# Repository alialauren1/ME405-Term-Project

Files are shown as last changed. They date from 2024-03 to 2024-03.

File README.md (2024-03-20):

# ME405-Term-Project

Our term project this quarter entails constructing a submersible chamber capable of reaching
specified depths. The system will operate in a closed loop, maintaining control until it 
reaches a desired pressure depth.

This project was intended for our senior project where. Dr. Ghalamchi wants to improve previous tests on waterproof drones that can take off from underwater to allow for a drone that can float on top of the water surface as well as have added support to be pushed up from underwater. The new design needs to be detachable from the built waterproof drone to compare its new features in tests. The propellers must also be above the water surface when the drone is idling on the water so that the efficiency of takeoff can be compared to the drone without the chamber in which the whole drone is submerged underwater upon takeoff.

Our project for ME 405 will be the system attached to this drone, enabling the drone to submerge underwater with a minimum depth of 5ft. While allowing for the system to resurface and position the propellers above the water's surface. 

Pressure can be directly correlated to depth, given a liquid's density.
   In order to simulate this system for our ME 405 Term Project, this system takes a desired pressure setpoint and controls a motor-driven syringe system to
   pressurize a chamber to the setpoint. It waits a period of time, as if it were underwater collecting data,
   and then returns to the initial pressure, as if it were returning to the water surface. 

## Hardware design
In Figure 1, we can see the internal system of the system. We have integrated Ametck Pittman's PG6712A077-R3 motor to a 50 CC syringe. Utilizing this motor, we've have attached a worm gear and gears to ensure sufficient torque to be generated. These gears are attached to a pinion
and aligned with a rack that allows for the syringe to be moved back and forth. This allows
for the system to achieve the desired weight to submerge the whole system.

The gears were selected from McMaster. This is so in the future, they can be ordered parts. For now, we used the CAD files to 3D print them for budget reasons. While sizing and choosing the number of teeth we would need for our system, we calculated to torque that the motor needed to have to overcome the friction force between the piston and syringe. This calculation is shown below. In the future, we can order a motor that is more selectively chosen using this information. However for now, we used the motor provided to us in lab. 

$F_r = T_A / R_A$

$T_A = F_R * R_A$

$T_B = T_A$

$T_C = (N_C / N_B ) * T_B$

$T_C = (N_C / N_B ) * (F_R * R_A)$

$T_C = (1/15) * (6 N) * (.0152 m)$

$T_C = (0.006 Nm) = (6 mNm)$ 

Doing these calculations led us to select appropriate gears for our system, ensuring that they can withstand the pressure encountered during operation while maintaining an ideal speed. Below shows a table of the parameters.  

| **Parameters** | Variable | Value | Units |
|:---:|:---:|:---:|:---:|
| **----Rack+Piston+Syringe--** |  **-------** |  **----** |  **----** |
| Force to overcome friction in tube | F_R | 6 | N |
| **----Gears--** |  **-------** | **-----** | **-----** |
| Radius Gear A | R_A | 0.0152  | m |
| Teeth Gear A | N_A | 17 | |
| Outer Diameter Worm Gear B | OD_B | 16 | mm |
| Teeth Worm Gear B | N_B | 15 | |
| Pressure Angle Worm Gear B | Phi_C | 20 |  degrees  |
| Outer Diameter Worm C | OD_C | 12 | mm |
| Pressure Angle Worm C | Phi_C | 20 |  degrees  |
| Teeth Worm C | N_C | 1 | |
| **-----Motor Parameters------**  | **--------** | **-----** |  **----** |
| Radius of Motor Gear | rm |  0.00662  | m |
| Motor Nominal Voltage | V_DC | 12 | V |



Figure 1. CAD: Internal system of our terms project with labels indicating parts of the system.



Figure 2. CAD: Secondary view of the internal system of our terms project with labels indicating parts of the system.

Screenshot 2024-03-19 at 6 15 07 PM

Figure 3. Gears, motor, and frame for the internal system.

The pressure sensor we selected is the SSCMANV030PA2A3 Honeywell Pressure Sensor. It measures absolute pressure, with a range from 0-30 psi. Is allows liquid media on the port, which will come of use in future quarters when we test our system underwater. 

Screenshot 2024-03-19 at 8 53 00 PM

Figure 4. SSCMANV030PA2A3 Honeywell Pressure Sensor



Figure 5. Hardware all connected



Figure 6A. System Connected to Bottom of Drone Body - View 1



Figure 6B. System Connected to Bottom of Drone Body - View 2

Screenshot 2024-03-19 at 8 43 37 PM

Figure 7. Overall View of Drone Body with Chamber 

### Schematic

The schematic below shows a very general diagram of how components are being powered and communicating with one another. 
The power supply provides power to the motor. The power supply was set to 12V with a 0.5 A current limit. 

Schematic

Figure 8. Schematic of components

## Software design
The main program uses three classes inside two tasks that multitask with one another. A detailed description of the software design can be found on our doxygen main page linked here: 
https://alialauren1.github.io/ME405-Term-Project/index.html#soft_org_sec

To measure pressure, we used a Honeywell Board Mount Pressure Sensor, which uses I^2C communication. A class was made to use this sensor. Details on how the data was collected and process is linked below. 
https://alialauren1.github.io/ME405-Term-Project/index.html#autotoc_md1

Attaching the sensor and the Ametek motor to our Nucleo, we were able to program both components to get a functioning product.

### Tasks and States
The Tasks and States used in the main program are shown in diagrams linked on the page below.
https://alialauren1.github.io/ME405-Term-Project/index.html#T_S_sec

## Testing and Results

### Preliminary
Our senior project requires our chamber to be able to acheive at minimum, 5 ft depth. Calculations were run, shown below, to determine the pressure that coincides with a depth of 5 ft in water. Being a little under 16.5 psi, we decided to run initial tests at 16.5 psi.

Screenshot 2024-03-19 at 9 05 30 PM

In order to test our project sensors and motor control, we ran multiple tests in order to find our optimal Kp value. The results are presented in the plot down below. This was preliminary testing. 

Screenshot 2024-03-17 at 10 32 32 PM

Figure 9. Plot of Pressure vs Time inside the syringe. Each line represents a different run of data collected while altering the Kp value.

During our testing, we initially set Kp to 5 (shown in blue) and then increased it to 10 (shown in orange). Observing the graph, it's evident that increasing the Kp value led to faster attainment of the target pressure of 16.5 [psi].

While testing to achieve for efficiency in reaching the desired pressure, it's essential to consider what our system will be attached to. Our system with the syringe and pressure sensor will be attached to a drone. Rapid pressure and volume changes may introduce a moment within the drone body, causing the drone to loose control. Therefore, we must weigh the trade-offs between achieving rapid pressure targets and maintaining system stability.

As we continue to test our project, further tests will be necessary to determine the optimal balance between speed, the system stability and accuracy. This process may involve fine-tuning parameters beyond just changing the Kp. This may incude making the chamber of the system bigger and other factors.

### Lab Demo Results and Functionality of Product
The below plot shows the pressure inside the syringe. The autonomous journey is one in which the system reaches the desired setpoint, waits for a duration, and then returns to the initial pressure. 



Figure 10. Plot of Pressure vs Time inside the syringe with a setpoint of 17 [psi].  

This journey mimics future developement of our larger senior project in which this pressure chamber will be attached to a drone. We anticipate it will be beneficial for some remote or signal to send a desired depth as the setpoint to the system, in which the chamber will submerge with the drone, going to that depth. It will remain there, possible to collect data, and then autonomously return to the surface. 
We are satisfied with the final results. The chamber is able to reach pressures higher than a pressure corresponding to 5ft, which was what we wanted to achieve.
It is also able to maintain the increase in pressure while the motor is turned off, which is a satisfying result. 

The system also works at lower than atmosphere pressures. In the plot below, the setpoint was chosen as 13 psi. However, in another test, we were able run the system with an even lower setpoint of 10 psi. Although this is less necessary to have, it is satisfying to see that ability. 

Screenshot 2024-03-19 at 8 38 33 PM

Figure 11. Plot of Pressure vs Time inside the syringe with a setpoint of 13 [psi].  

## What we have learned
Designing this system taught us how important it is to design and test early. 
Although most of the system was done with a reasonable amount of time, we were faced with issues causing the system to take longer to complete than anticipated.

### 3D Printing
While 3D printing gears and housing system for our project we learned that tolerances while creating parts is harder to achieve. When 3D printing the gears it was harder to align the gears causing the small gears to slip and not allowing for our system to be as efficient as it can be.

Note: We are saving our used PLA parts to find a place to recycle them. 

Screenshot 2024-03-19 at 6 14 47 PM

Figure 12. Collection of gears tested

### Software and Sensors
We learned that the data being output from our pressure sensor was in counts. This led to the creation of a definition in our PressureSensor class to interpret the counts into a unit of measurement that could be easily interpretted, that being [psi]. Since our Closed-Loop Controller class uses the pressure sensor output in counts to correct for a desired pressure, an additional definition was made to interpret user desired setpoint input from [psi] to counts. 

## Safety
Our project prioritizes user safety through thoughtful design considerations. By utilizing small gears, we have effectively reduced the risk of injuries to the user. Once the system has been fully assembled, all moving components and electrical elements will be enclosed and inaccessible to the user. This design ensures that users are protected from potential hazards during the system's operation.

## Bugs and Future Work

We would also like to fix our code in Task2 State 3 where there is a break in data collection between the chamber resting at a higher pressure and then returning to its original pressure. As shown on the plot in the "Lab Demo Results" section, there is a small duration of time in which no data is collected. That is state 3, whilst counter_s3 is between 1 and 3. We tried removing this portion and only having state 3 reset the setpoint to initial pressure in one count but it did not initially work and we have run out of time to work on the code. So, for now, there is that small time duration blip in the data.  

In the future we would like to implement a third task into our main program that is a user interface for the pressure setpoint. 
The user could select from a range of setpoint options and the system would adjust the pressure in the chamber accordingly. 
This task would multitask with the other two tasks and allow for the user to input a setpoint whenever they want whilst the program runs. 

We plan to build a larger waterproof chamber to encompass components similar to those used in project. This will allows us to test the systems depth control abilities in actual water. We look forward to the continuation of this project and appreciate all that it has taught us so far. 

## Additional files

Pressure sensor datasheet:
[SSCMANV030PA2A3 Honeywell.pdf](https://github.com/alialauren1/ME405-Term-Project/files/14630972/SSCMANV030PA2A3.Honeywell.pdf)

I2C Communications with Honeywell Pressure Sensors:
[sps-siot-i2c-comms-digital-output-pressure-sensors-tn-008201-3-en-ciid-45841.pdf](https://github.com/alialauren1/ME405-Term-Project/files/14630975/sps-siot-i2c-comms-digital-output-pressure-sensors-tn-008201-3-en-ciid-45841.pdf)

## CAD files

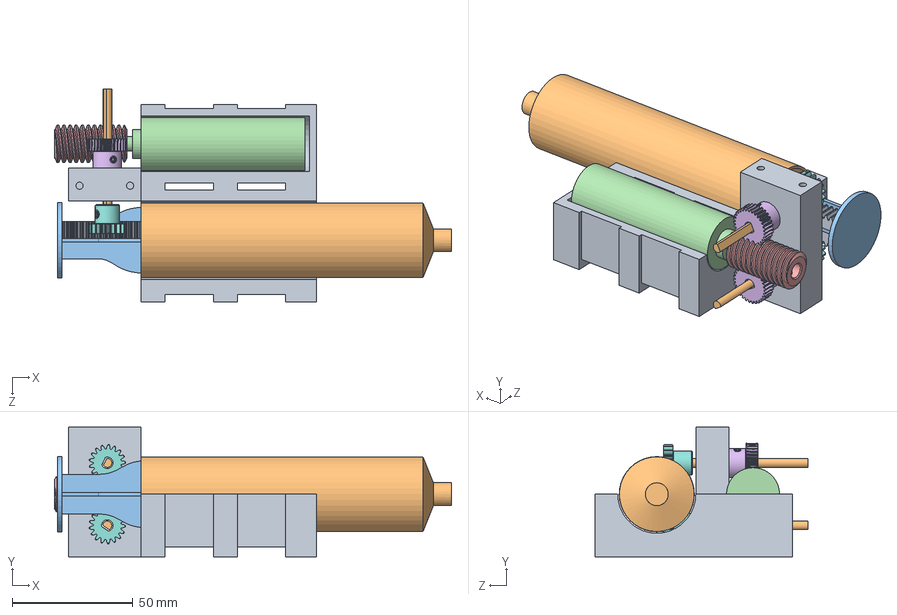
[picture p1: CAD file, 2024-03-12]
CAD_ME405/Buoyancy Chamber Assembly.SLDASM
164.7 x 53.7 x 88.3 mm
Component_Stucture_copy
Copy of Part2^Buoyancy Chamber Assembly
Copy of Part3^Buoyancy Chamber Assembly
Motor_body
57545K736_Metal Worm Gear (1) x 2
57545K624_Steel Worm
2664N437_Metal Gear - 20 Degree Pressure Angle x 2
2485N214_Metal Gear Rack - 20 Degree Pressure Angle x 2
6mm bar x 2

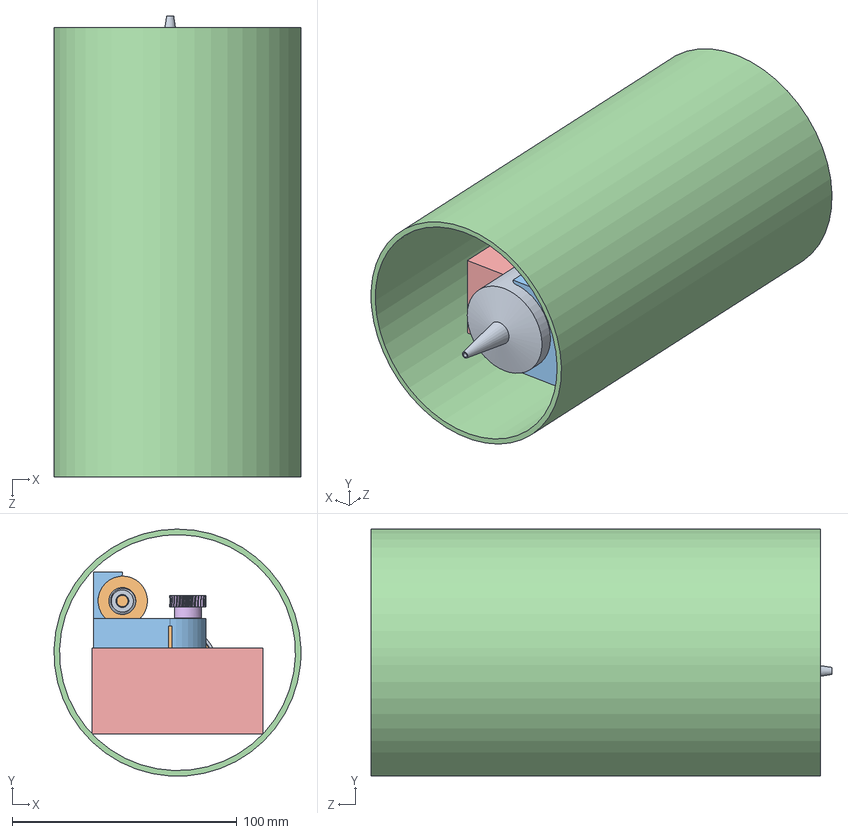
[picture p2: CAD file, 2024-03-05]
CAD_ME405/syring_1.SLDASM
109.9 x 109.9 x 205.0 mm
syringe_out_1
syring_push_1
6mm bar x 2
57545K737_Metal Worm Gear (1) x 2
2485N242_Metal Gear Rack - 20 Degree Pressure Angle x 2
2664N411_Metal Gear - 20 Degree Pressure Angle x 2
57545K624_Steel Worm
Motor_body
Motor_holder

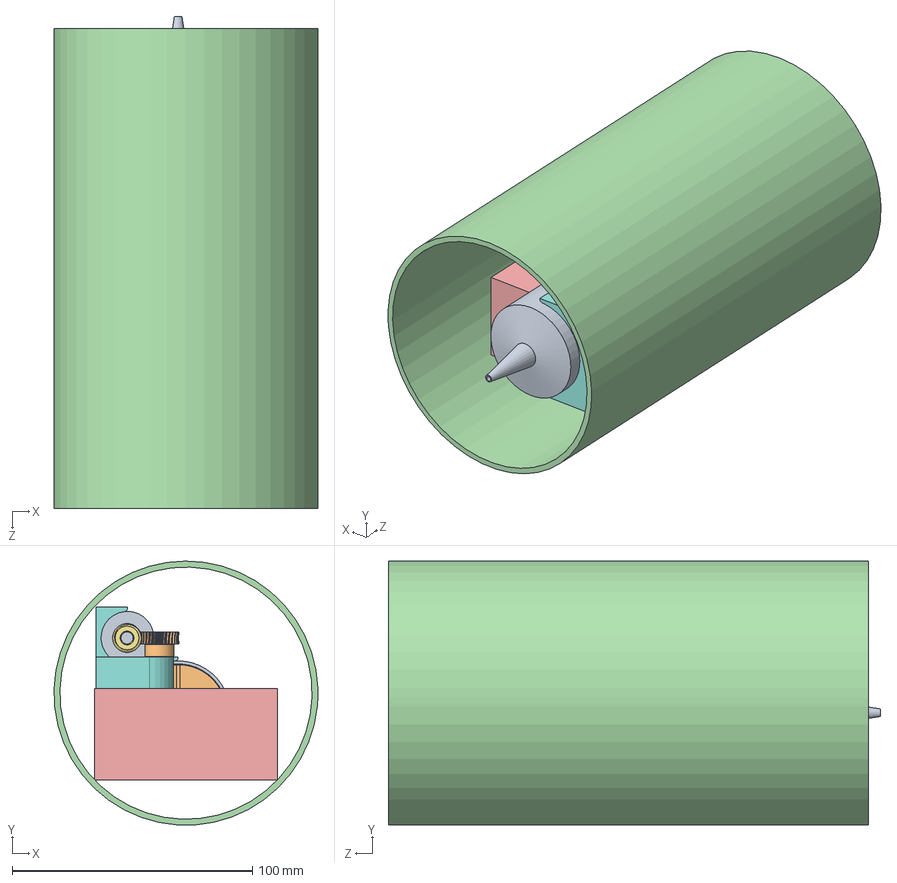
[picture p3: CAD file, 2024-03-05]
CAD_ME405/syring_1_V3.SLDASM
109.9 x 109.9 x 205.0 mm
syringe_out_1
syring_push_1
6mm bar
2664N411_Metal Gear - 20 Degree Pressure Angle
57545K624_Steel Worm
Motor_holder_V3
Motor_body
57545K737_Metal Worm Gear (1)
rack_V3

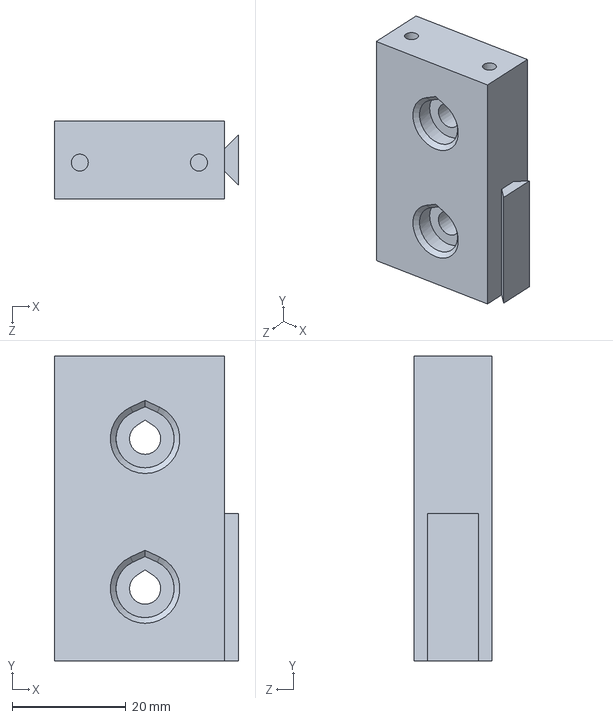
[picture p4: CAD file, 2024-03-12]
CAD_ME405/Gear_holder.SLDPRT
32.5 x 53.7 x 13.7 mm

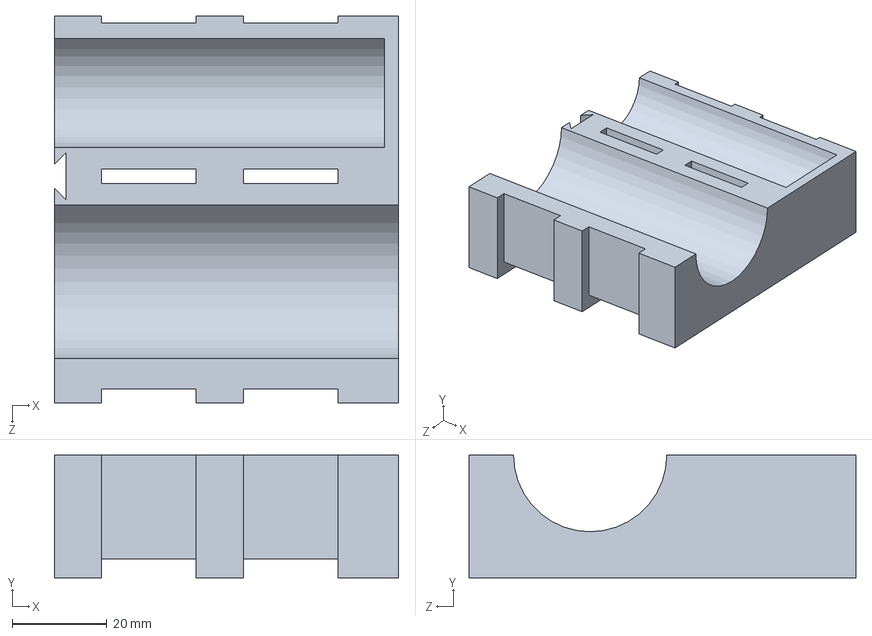
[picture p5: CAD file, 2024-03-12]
CAD_ME405/Motor_Syringe_Holder.SLDPRT
72.8 x 26.0 x 81.8 mm

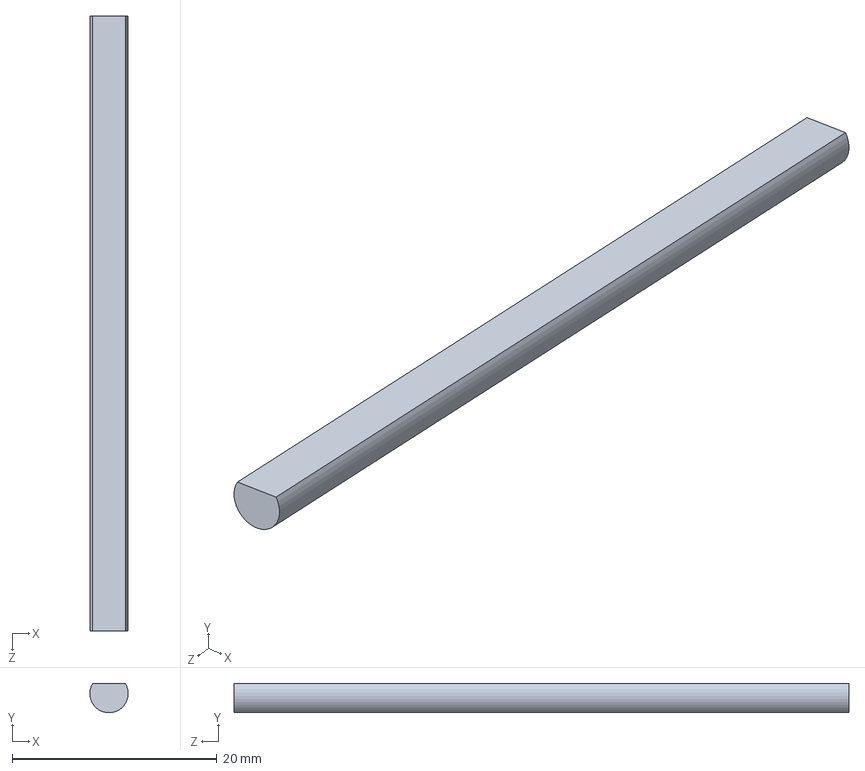
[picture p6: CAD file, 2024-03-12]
CAD_ME405/6mm bar.SLDPRT
3.75 x 2.87 x 60.0 mm

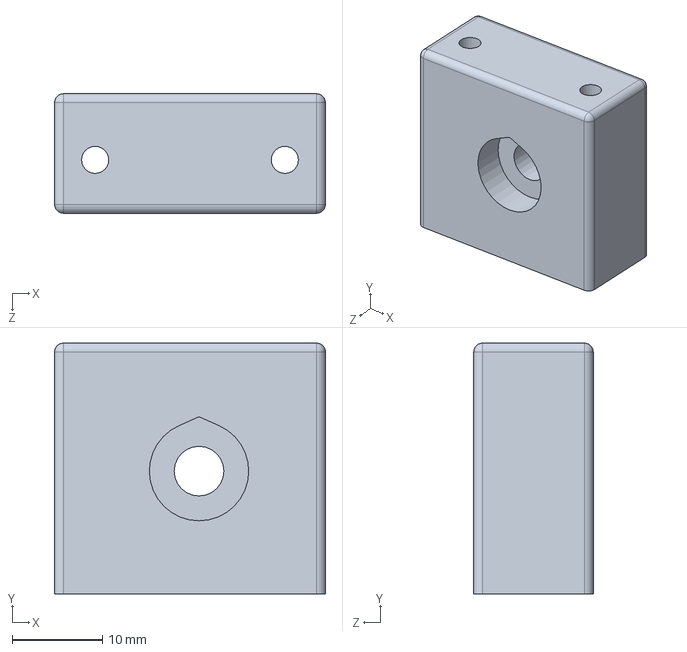
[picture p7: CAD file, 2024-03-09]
CAD_ME405/Component_Structure_Top.SLDPRT
30.0 x 27.8 x 13.2 mm

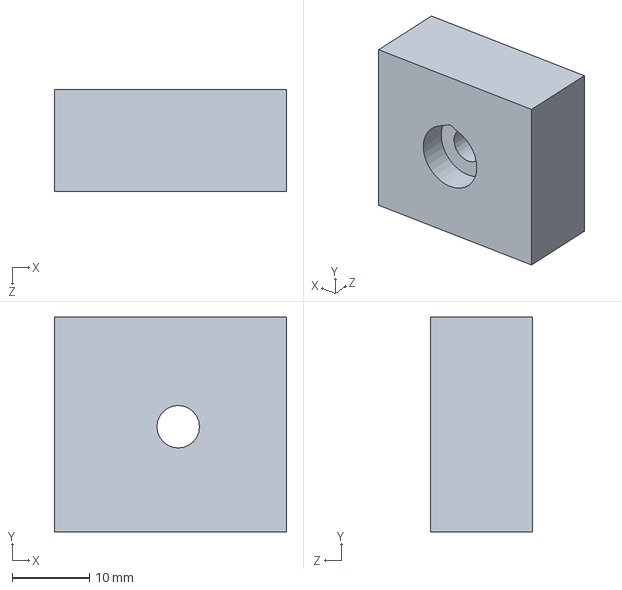
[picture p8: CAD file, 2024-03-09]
CAD_ME405/Component_Structure_Top_Attactment.SLDPRT
30.0 x 27.8 x 13.2 mm

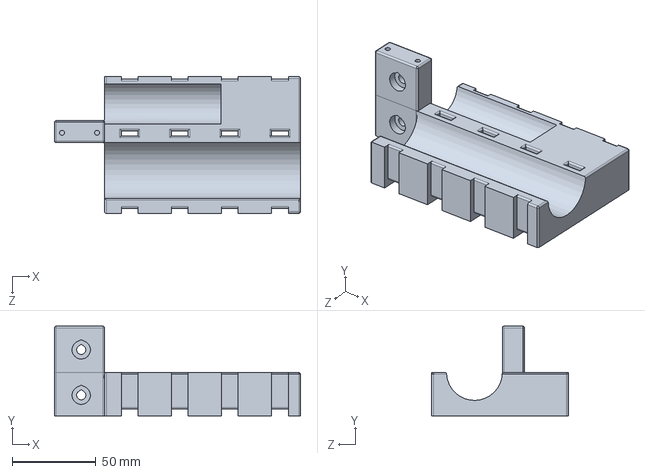
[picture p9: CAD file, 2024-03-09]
CAD_ME405/Component_Stucture.SLDPRT
147.3 x 53.7 x 81.8 mm

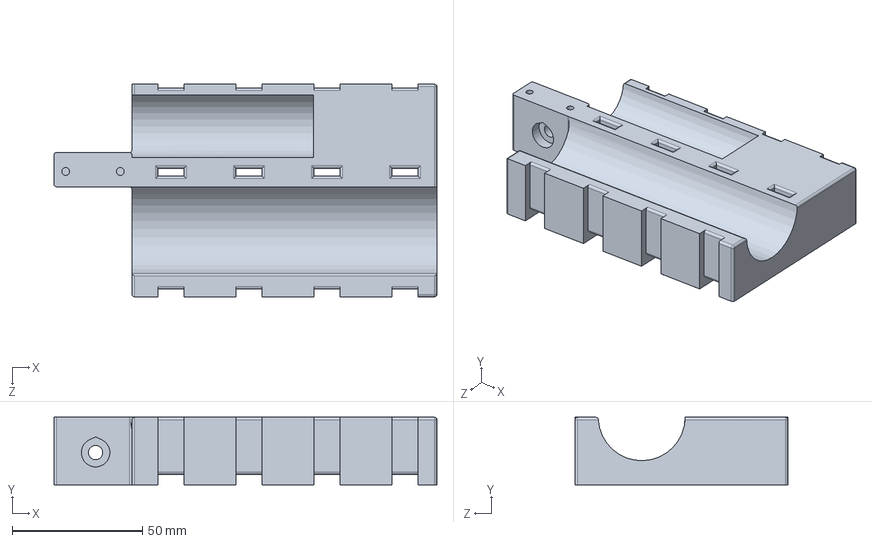
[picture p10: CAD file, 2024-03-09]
CAD_ME405/Component_Structure_Base.SLDPRT
147.3 x 26.0 x 81.8 mm

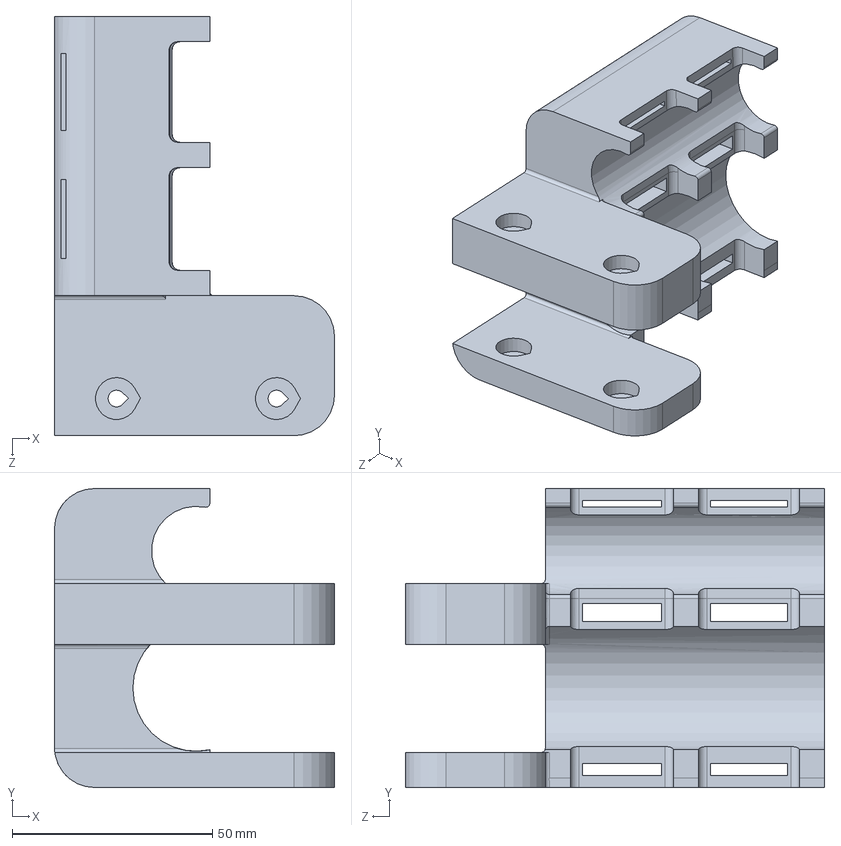
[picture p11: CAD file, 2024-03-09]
CAD_ME405/Part1^syring_1_V3.SLDPRT
70.0 x 74.7 x 104.8 mm

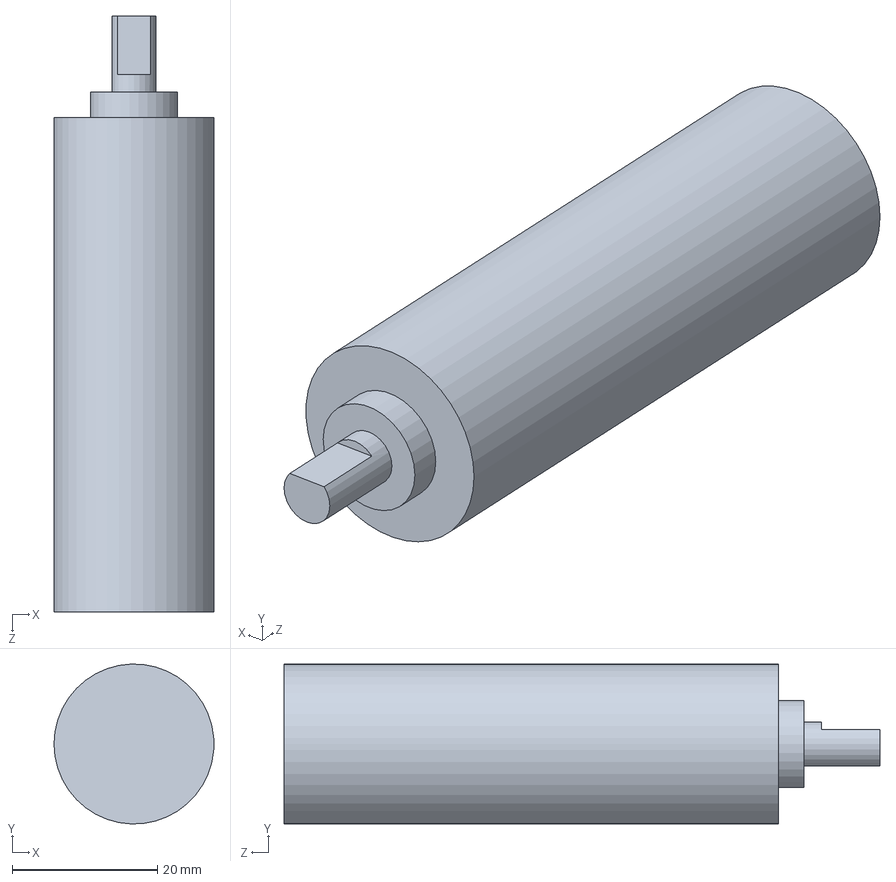
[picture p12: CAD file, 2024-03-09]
CAD_ME405/Motor_body.SLDPRT
22.0 x 22.0 x 81.9 mm

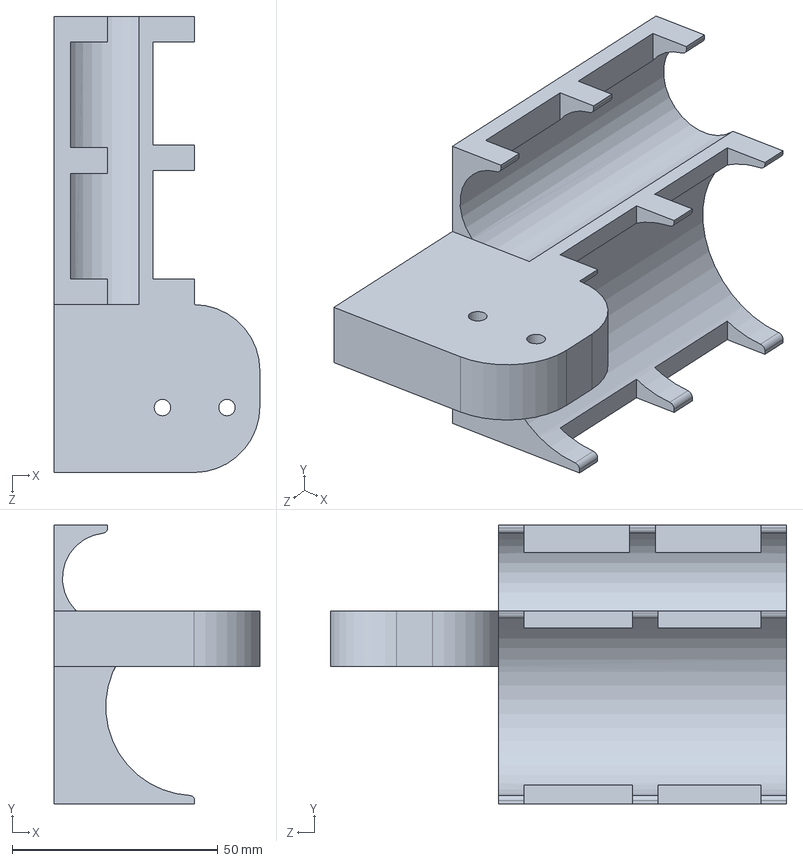
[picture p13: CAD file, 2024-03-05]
CAD_ME405/Motor_holder.SLDPRT
50.0 x 67.7 x 110.8 mm

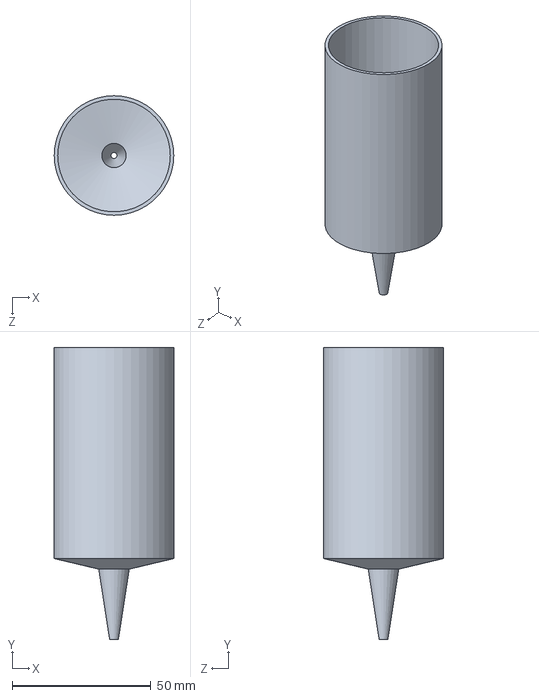
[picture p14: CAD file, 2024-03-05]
CAD_ME405/syringe_out_1.SLDPRT
43.2 x 105.4 x 43.2 mm

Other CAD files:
CAD_ME405/Motor_holder_V3.SLDPRT
CAD_ME405/rack_v1 (2).SLDPRT
CAD_ME405/rack_V3.SLDPRT
CAD_ME405/syring_push_1.SLDPRT
CAD_ME405/2485N236_Metal Gear Rack - 20 Degree Pressure Angle.SLDPRT
CAD_ME405/2485N242_Metal Gear Rack - 20 Degree Pressure Angle.SLDPRT
CAD_ME405/2664N411_Metal Gear - 20 Degree Pressure Angle.SLDPRT
CAD_ME405/2664N441_Metal Gear - 20 Degree Pressure Angle.SLDPRT
CAD_ME405/57545K624_Steel Worm.SLDPRT
CAD_ME405/57545K627_Steel Worm.SLDPRT
CAD_ME405/57545K737_Metal Worm Gear (1).SLDPRT
CAD_ME405/57545K744_Metal Worm Gear.SLDPRT
CAD_ME405/6mm bar_V1.SLDPRT
CAD_ME405/Holder.SLDPRT
CAD_ME405/Nucleo.SLDPRT
CAD_ME405/Part1^syring_1_V2.SLDPRT
CAD_ME405/rack_v1 (1).SLDPRT
CAD_ME405/syring_1_V2.SLDASM
STL/2485N242_Metal Gear Rack - 20 Degree Pressure Angle.STL
STL/2664N411_Metal Gear - 20 Degree Pressure Angle.STL
STL/57545K624_Steel Worm.STL
STL/57545K737_Metal Worm Gear (1).STL

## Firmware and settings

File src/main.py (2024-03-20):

"""!
@file main.py
    This file runs two tasks, using two intershared variables and two queues.
    Task 1 processes and prints the data from the queues.
    Task 2 stores the data from the sensor into the queues.
    
    This file was modified from basic_tasks.py, author: JR Ridgely.
    The copyright from the basic_tasks file is included below. 
    
@author Alia Wolken, Eduardo Santos, Andrew Jwaideh
@date   2024-March-19

@copyright (c) 2015-2021 by JR Ridgely and released under the GNU
    Public License, Version 2. 
"""

import gc
import utime
import pyb
import cotask
import task_share
import Closed_Loop_Controller

from motor_driver import motordriver
from Closed_Loop_Controller import Controller
from pressure_sensor import PressureSensor

def task1_print(shares):
# convert, and print data
    """!
    Task which:
    - Gets time and pressure out of a queue and the current Task 2 value out of a share.
    - Converts pressure from units of counts to [psi] and displays value along with corresponding depth underwater in [ft] and time duration.
    @param shares: A tuple of a share and queue from which this task gets data
    """
    # Get references to the share and queue which have been passed to this task
    qTime, qPos, share_init_p, share_off = shares
        
    sensor_obj = PressureSensor(0,0,0)
    
    T1_state = 1
    S1_print = 1

    while True:
        
        if (T1_state == S1_print): # STATE 1: Done with Controller, Print Vals
            
            time = qTime.get() # Pull Time from Queue
            pos = qPos.get() # Pull Pressure from Queue

            pos_raw = (pos) 
            pressure, pressure_diff, depth, init_p  = sensor_obj.RawtoData_P(pos_raw) # Converts Pressure from [counts] to [psi] 
            share_init_p.put(init_p) 
            print(time,pressure,depth) # Prints time, pressure [psi] and depth [ft]
            
            T2_state = share_off.get() # Determine Task2's state
            if T2_state == 3: # Task2's state 3 indicates no data collection occuring, therefore, no printing needed
                T1_state = 2
            
        elif (T1_state == 2): # STATE 2: Dont Print Vals (no vals to print)
            T2_state = share_off.get() # Determine Task2's state
            if T2_state == 1: # Task2's state 1 indicates data is being collected
                T1_state = 1 # Transition back to printing data
            
        yield T1_state
            
        
def task2_get(shares):
    """!
    Task that:
    - Converts desired setpoint from units of [psi] to counts using Pressure Sensor Class
    - Reads pressure sensor data in units of counts from Pressure Sensor Class.
    - Runs closed-loop controller with pressure counts comparing against setpoint to send motor PWM commands.
    - Puts time duration and pressure into queue 
    @param shares: A tuples of a share and queue from which gets data.
    """
    
    # get data
    qTime, qPos, share_init_p, share_off = shares[0], shares[1], shares[2], shares[3]

    moe2 = motordriver (pyb.Pin.board.PA10, pyb.Pin.board.PB4, pyb.Pin.board.PB5, 3)
    
    setpoint_p = 10 # Setpoint in [psi]
    sensor_obj = PressureSensor(setpoint_p,0,0) # Conversion in PressureSensor class from [psi] to counts
    setpoint_raw = sensor_obj.PtoRawP(setpoint_p) # Setpoint in [counts]
    
    # Paramters for the contoller
    Kp = 2
    controller_obj2 = Controller(Kp, setpoint_raw)
    
    T2_state = 1
    S1_data = 1
    S2_off = 2
    S3_goback = 3
    counter = 0
    counter_s3 = 0
    final_counter = 0
    key = 0
    
    while True:
        
        if (T2_state == S1_data): # Collect Data & Run Closed Loop Controller
            initialP = share_init_p.get() # Initial Pressure taken during initialization of PressureSensor Class
            
            reader_p_value, temp_val = sensor_obj.readP_Raw() # Reads Raw P & T values
            PWM, time_passed, measured_output = controller_obj2.run(reader_p_value) # Runs Closed-Loop Controller 
            moe2.set_duty_cycle(-PWM) # Ajusts motor 2 postion 
            
            qTime.put(time_passed)       # stores time passed in queue to print 
            qPos.put(measured_output)    # stores measured pressure [counts] in queue to print 
            
            # If Desired Pressure is Reached
            if setpoint_raw-6 <= reader_p_value <= setpoint_raw+6: # Allowable range to consider "reaching" setpoint
                #print('REACHED SETPOINTT!!')
                T2_state = 2 
                key = 1
            
            # If System has been Returned to Initial Pressure
            if (initialP-6 <= reader_p_value <= initialP+6) & key == 1: # Allowable range to consider "reaching" return pressure
                moe2.set_duty_cycle(0) # turn motor off
                PWM, time_passed, measured_output = controller_obj2.run(reader_p_value) 
                qTime.put(time_passed)       # stores time passed in queue to print 
                qPos.put(measured_output)    # stores measured pressure [counts] in queue to print l
                final_counter += 1       
                if final_counter == 20:      # collects 20 more data points at returned pressure
                    T2_state = 4
                
        elif (T2_state == S2_off): # time with motor off, collecting data
            moe2.set_duty_cycle(0)
            PWM, time_passed, measured_output = controller_obj2.run(reader_p_value)
            qTime.put(time_passed)         # stores time passed in queue to print 
            qPos.put(measured_output)      # stores measured pressure [counts] in queue to print 
    
            counter += 1                   # collects 20 more data points at setpoint pressure
            if counter == 20:  
                T2_state = 3               
                share_off.put(T2_state)
                counter = 0 # clear counter
                
        elif (T2_state == 3): # time with motor off, not collecting data, resets setpoint to initial pressure 
            counter_s3 += 1
            if counter_s3 == 4: # only run for a few counts
                controller_obj2.set_setpoint(initialP)
                T2_state =1
                share_off.put(T2_state)
                counter_s3 = 0

        elif (T2_state == 4): # does nothing
            pass

        yield T2_state

# This code creates a share, a queue, and two tasks, then starts the tasks. The
# tasks run until somebody presses ENTER, at which time the scheduler stops and
# printouts show diagnostic information about the tasks, share, and queue.
if __name__ == "__main__":
    print("Testing ME405 stuff in cotask.py and task_share.py\r\n"
          "Press Ctrl-C to stop and show diagnostics.")
    
    qTime = task_share.Queue('L', 100, thread_protect=False, overwrite=False,
                          name="Queue Time")
    qPos = task_share.Queue('L', 100, thread_protect=False, overwrite=False,
                          name="Queue Pos")
    init_p = task_share.Share('h', thread_protect=False, name="initial pressure")
    share_off = task_share.Share('h', thread_protect=False, name="Share Off")
    
    # Create the tasks. If trace is enabled for any task, memory will be
    # allocated for state transition tracing, and the application will run out
    # of memory after a while and quit. Therefore, use tracing only for 
    # debugging and set trace to False when it's not needed
    task1 = cotask.Task(task1_print, name="Task_1", priority=1, period=60,
                        profile=True, trace=False, shares=(qTime, qPos, init_p, share_off))
    task2 = cotask.Task(task2_get, name="Task_2", priority=2, period=50,
                        profile=True, trace=False, shares=(qTime, qPos, init_p, share_off))
    
    cotask.task_list.append(task1)
    cotask.task_list.append(task2)
    
    # Run the memory garbage collector to ensure memory is as defragmented as
    # possible before the real-time scheduler is started
    gc.collect()

    # Run the scheduler with the chosen scheduling algorithm. Quit if ^C pressed
    while True:
        try:
            cotask.task_list.pri_sched()
        except KeyboardInterrupt:
            break

    # Print a table of task data and a table of shared information data
    print('\n' + str (cotask.task_list))
    print(task_share.show_all())
    print('') 

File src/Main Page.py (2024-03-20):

"""! \mainpage 
   \section intro_sec Introduction
   
   The purpose of this project was to develop a preliminary depth control chamber.
   
   Pressure can be directly correlated to depth, given a liquid's density.
   This project takes a desired pressure setpoint and controls a motor-driven syringe system to
   pressurize a chamber to the setpoint. It waits a period of time, as if it were underwater collecting data,
   and then returns to the initial pressure, as if it were returning to the water surface. 
 
   \section soft_org_sec Software Description and Organization
   
   The main program uses three classes to do our desired function.
   It contains multiple tasks in which it multitasks between one another. 
   
   Following a brief description of the main program, the classes used are mentioned. 
   
   ## Main Program
   The main program initially collects a setpoint pressure, which is the desired pressure the user wants to go to.
   Then, as the program multitasks, is uses the Pressure Sensor class to essentially interpret and collect pressure values.
   It works with the Closed-Loop Controller class to run the motor driver based on calculated error between setpoint and current pressure.
   The program with run the controller until reaching the setpoint, in which it turns the motor off for a time duration.
   Then, the program will use both the Pressure Sensor and Closed-Loop Controller classes again to return the chamber to the initial pressure from start up.
   
   Throughout the duration of the program, if there are pressure values being collected, there will be values printed.
   This occurs by the program multitasking between data collection and printing. 
   
   ##Pressure Sensor Class
   To measure pressure, we used a Honeywell Board Mount Pressure Sensor, which uses I^2C communication. The sensor transmits data in byte arrays. The first byte being status, next two being pressure, and following two being temperature. A PressureSensor class was created to process the data from bytes into counts and then interpretable values of pressure in [psi] and temperature in [Farenheight].

   Two types of data were collected. One being pressure, our primary focus, and the other temperature, for future use. You can read more about our pressure sensor and its I^2C communication using the links included at the bottom of the readme. 
    
 * def __init__:
         Initialize the PressureSensor Object.
         Collect initial data values for status and initial pressure. 
 * def readP_Raw:
         Reads Raw Status, Pressure, and Temperature Data from Sensor
 * def PtoRawP:
         Converts setpoint pressure from units of psi to counts.
 * def RawtoData_P:
         Converts raw pressure data in units of counts to [psi].
         Then pressure difference from initial pressure and thus displacement depth
 * def RawtoData_T:
         Converts raw pressure data in units of counts to [Fahrenheit].
    
     ### Status
    To interpret the status output from the pressure sensor, the table below was used, provided from the manual, "I^2C Communications with Honeywell Digital Output Pressure". 

    <img width="294" alt="Screenshot 2024-03-17 at 9 48 11 PM" src="https://github.com/alialauren1/ME405-Term-Project/assets/157066441/f21555c3-b900-4082-98ba-afea877355a0">

    The class was written to always print the status upon calling it. Throughout our use and application of the class, the status of the sensor was always S1 = 0 and S0 = 0, indicating we were in a normal operation, whilst collecting valid data.  

    ### Pressure
    To calculate the pressure from the digital output, the pressure sensor transfer function shown below was used, also provided from the manual, "I^2C Communications with Honeywell Digital Output Pressure". The equation was rearranged to solve for Pressure. 

    <img width="326" alt="Screenshot 2024-03-17 at 9 38 54 PM" src="https://github.com/alialauren1/ME405-Term-Project/assets/157066441/e8322335-e550-4d0f-b144-daa90d571818">

    Where,

    <img width="347" alt="Screenshot 2024-03-17 at 9 41 27 PM" src="https://github.com/alialauren1/ME405-Term-Project/assets/157066441/81dee95d-3d2a-44a9-8cc6-a6c065db89b8">

    ### Temperature
    The temperature conversion function shown below was also provided in the Honeywell I^2C manual. Although, it was modified to convert the temperature into Fahrenheit. 

    <img width="249" alt="Screenshot 2024-03-17 at 9 46 18 PM" src="https://github.com/alialauren1/ME405-Term-Project/assets/157066441/79dcab9f-85fb-4055-beed-cf1e42050b7f">
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

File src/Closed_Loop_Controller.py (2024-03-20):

"""!
@file Closed_Loop_Controller.py
    This file is a class that implements a closed loop system, with proportional control.
    It allows for initialization of the desired Kp and setpoint.
    There are also the optinos to set a new Kp and setpoint when corresponding definitions are called. 
  
@author Alia Wolken, Eduardo Santos, Andrew Jwaideh
@date   2024-March-15 
"""

import utime
import cqueue

class Controller:
    """!
    This class represents a closed-loop contoller for the system. 
    @author Alia Wolken, Eduardo Santos, Andrew Jwaideh
    """
    
    def __init__(self, kp, set_point):
        """!
        Inits the Controller object with the provided proportional gain and set points.
        
        @param Kp (float): The proportinal gain of the controller.
        @param set_point (float): Is the desired setpoint of the system.
        @param start (int): The initial time of when the controller starts.
        """
         self.kp = float(kp)
         self.set_point = float(set_point)
         self.start = utime.ticks_ms()
         
    def run(self, measured_output):
        """!
        Runs the controller and calculation for the actual values based by the measured output.
        
        @param measured_output (float): The measured output of the system.
        @param return: A tuple containing the actual value and time that has passed.
        """
        err = self.set_point - measured_output # Calculates error 
        actuation = self.kp*err 
        current_time = utime.ticks_ms()
        self.time_passed = utime.ticks_diff(current_time, self.start)
        return actuation, self.time_passed, measured_output
        
    def set_setpoint(self, desired_set_point):
        """!
        Takes in a desired set point. 
        Sets new setpoint for class
        
        @param desired_set_point: The new setpoint
        """
        self.set_point = float(desired_set_point) # To set a new setpoint for class
        
    def set_Kp(self, desired_Kp):
        """!
        Takes in a desired Kp value. 
        Sets new Kp for class
        
        @param desired_Kp: The new kp value
        """
        self.kp = desired_Kp # To set a new kp for class
        

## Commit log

2024-03-02 SW files
    [57655K52_14-1-2 Degree Pressure Angle Plastic Gear.SLDPRT, 57655K63_14-1 2 Degree Pressure Angle Gear Rack.SLDPRT, 6mm bar.SLDPRT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]
2024-03-07 Working on pressure sensor
2024-03-07 UPDATED CAD
    [2664N411_Metal Gear - 20 Degree Pressure Angle.SLDPRT, 57545K624_Steel Worm.SLDPRT, 57545K737_Metal Worm Gear (1).SLDPRT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]
2024-03-08 Cutout Update
    [Part1^syring_1_V3.SLDPRT]
2024-03-08 more updates
    [syring_1_V2.SLDASM]
2024-03-09 Updates to CAD
    [Buoyancy Chamber Assembly.SLDASM, Component_Stucture.SLDPRT, Motor_body.SLDPRT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]
2024-03-09 put sensor collection into a class
2024-03-09 created new preliminary file
    Need to read pressure data before making a class for it
2024-03-10 working on a class for the sensor
2024-03-11 changed motor pins
2024-03-12 Setpoint Updates
    Input setpoint can now be a desired pressure value and the class will convert it to raw counts for analysis
2024-03-12 fixed a lil error
    [main.py, pressure_sensor.py]
2024-03-12 temp and pressure connected outputs
2024-03-12 final updates for the night
    Printed data should be in psi
2024-03-14 Update Data Plots.xlsx
    [Data Plots.xlsx]
2024-03-18 Organized files
    [2485N242_Metal Gear Rack - 20 Degree Pressure Angle.STL, 2664N411_Metal Gear - 20 Degree Pressure Angle.STL, 57545K624_Steel Worm.STL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]
2024-03-19 working on main page doxygen to insert images
2024-03-20 Update README.md
    added schematic
2024-03-20 schematic section
2024-03-20 renamed file
    [Data Plots.xlsx]
